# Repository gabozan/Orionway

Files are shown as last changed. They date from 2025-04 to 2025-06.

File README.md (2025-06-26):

<p align="center">
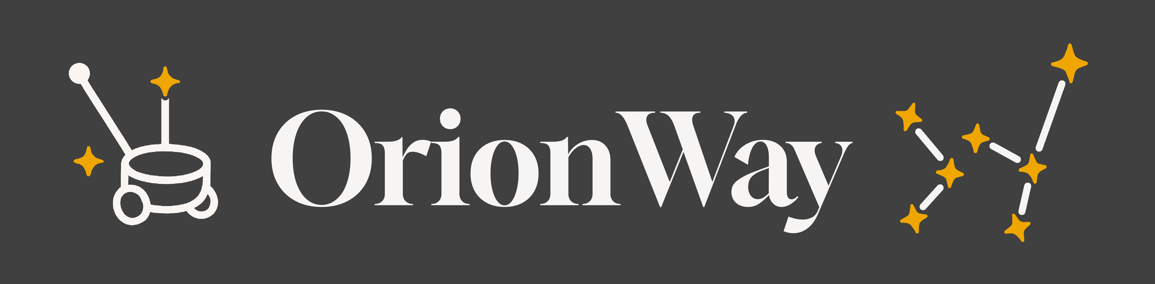
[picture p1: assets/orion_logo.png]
Logo Orionway
  
</p>

# OrionWay:  El guia robot per a trobar el teu camí 🤖👨‍🦯
&nbsp;&nbsp;&nbsp;&nbsp;

OrionWay és un **robot guia** dissenyat per acompanyar persones amb **discapacitat visual** en **entorns segurs**, com el campus de la Universitat Autònoma de Barcelona (UAB).

El projecte combina sensors i visió per computador per oferir assistència en el desplaçament, evitant perills com barreres, persones o passos de zebra. L’usuari mantindrà contacte amb el robot durant els trajectes, detectant quan el robot es desvia, dirigint-lo manualment o utilitzant-lo per identificar objectes desconeguts. L’objectiu és oferir una alternativa intermèdia entre un gos guia i el bastó blanc, combinant la seguretat i intuïció d’ambdós.

*El logotip d’OrionWay representa les inicials OW en codi Braille: ⠕⠺*

---

> [!CAUTION]
> Orionway és un prototip experimental desenvolupat en un entorn acadèmic i no està certificat per a ús assistencial en entorns reals. El seu ús com a substitut d’un gos guia o bastó blanc no està recomanat en entorns no controlats.

## 🙌 Autors
  | Nom             | NIU         |
|----------------------|-------------|
| Albert Capdevila Estadella                     | 1587933            |
| Levon Kesoyan Galstyan                      |  1668018           |
| Luis Martínez Zamora                     | 1668180            |
| Sebastian Malbaceda                      | 1681519            |
|  Gabriel Rios Sanchez                    |  1671177           |

## 🤝 Suport

### Agraïment especial
Gràcies a **Sergio Alamar**, humorista i exjugador de la selecció espanyola de futbol paralímpic, per compartir amb nosaltres la seva experiència directa com a persona cega. La seva col·laboració ens ha ajudat a identificar detalls essencials i a enfocar millor el desenvolupament d’OrionWay per fer-lo realment útil en situacions del dia a dia.

Si voleu conèixer més la seva història: [Article de La Vanguardia](https://www.lavanguardia.com/local/valencia/20250329/10522940/ciego-gracioso-sergio-alamar-comico-exolimpico.html)



### Institucions
* [Escola Enginyeria - UAB](https://www.uab.cat/ca/enginyeria)
* [UAB Open Labs](https://webs.uab.cat/openlabs/)

### Professorat
* Fernando Luis Vilariño Freire
* Vernon Stanley Albayeros Duarte
* Carlos Garcia Calvo

## 📚 Taula de continguts

- [🎥 Video demostració](#-video-demostració)
- [💫 Funcionalitats del robot OrionWay](#-funcionalitats-del-robot-orionway)
- [⚙️ Arquitectura i hardware](#️-arquitectura-i-hardware)
- [🤯 Aportacions destacades](#-aportacions-destacades-amazing-contributions)
- [🖥️ Esquemes de software](#️-esquemes-de-software)
- [🖧 Esquema de hardware](#-esquema-de-hardware)
- [📋 Requisits i instalació](#requisits-i-instalació)
- [🧪 Tests i millores](#-tests-i-milllores)
- [📚 Bibliografia i recursos](#-bibliografia-i-recursos)
- [📄 Llicència](#-llicència)

## 🎥 Video demostració
<a href="https://www.youtube.com/watch?v=D7q8VTSx6Zk">
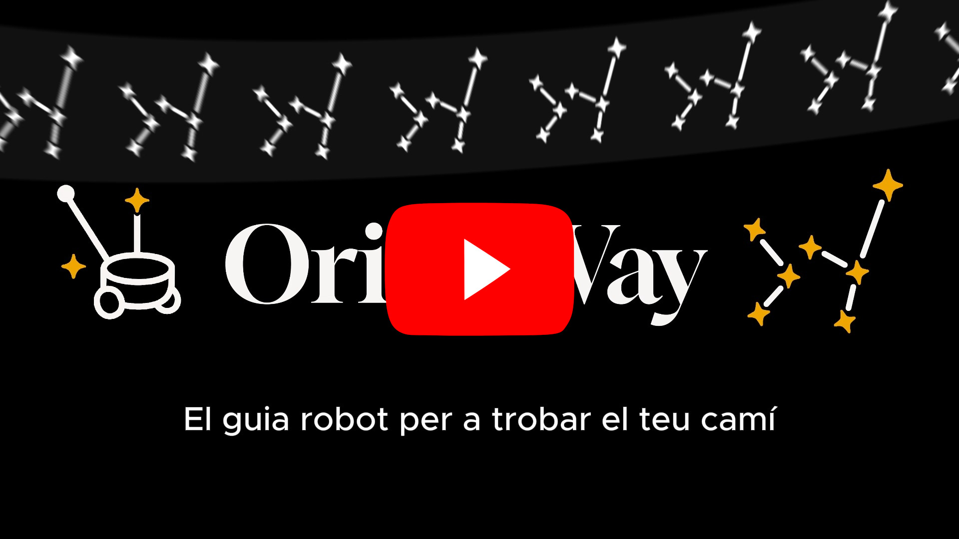
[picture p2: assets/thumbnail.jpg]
  
</a>

## 💫 Funcionalitats del robot OrionWay

| **Funcionalitat** | **Demostració** |
|---|---|
| **Detecció i reacció a obstacles immediats**<br>Mitjançant els tres sensors d'ultrasons situats al cos del robot i connectats a la placa Arduino, aquest serà capaç de detectar elements propers i modificar la trajectòria dels motors per tal d'esquivar-los. Ha de ser una funcionalitat molt ràpida i eficient, per tal d'aconseguir el millor temps de reacció. |  |
| **Detecció i reacció a passos de zebra amb semàfors**<br>Mitjançant la càmera i un model de visió per computador, podrem saber l'orientació dels passos de zebra propers, a més de detectar si els seus semàfors es troben en verd o en vermell. Això permetrà encarar el pas de zebra i creuar-lo quan pertoqui, evitant el perill. |  |
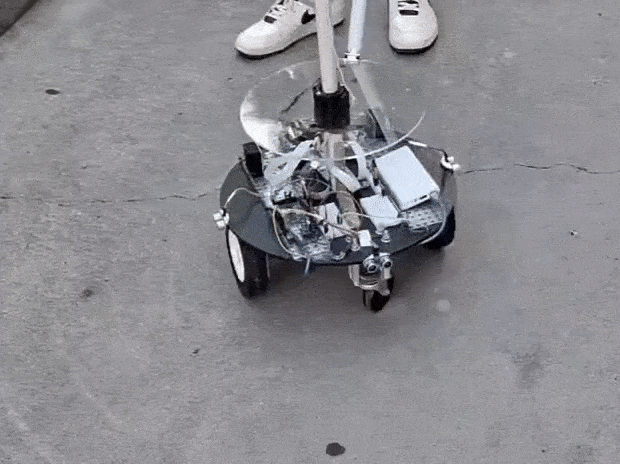
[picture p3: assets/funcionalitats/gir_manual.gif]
| **Dirigir manualment el robot en qualsevol moment**<br>En qualsevol moment dins el guiatge del robot, l'usuari podrà prémer els botons del mànec per a forçar manualment girs a la dreta o a l'esquerra. **IMPORTANT** Aquesta funcionalitat no tindrà més prioritat que les dues funcionalitats anteriors, és a dir, si a l'esquerra del robot es troba un obstacle immediat o un pas de zebra amb semàfor en vermell, el robot es detindrà. |  |
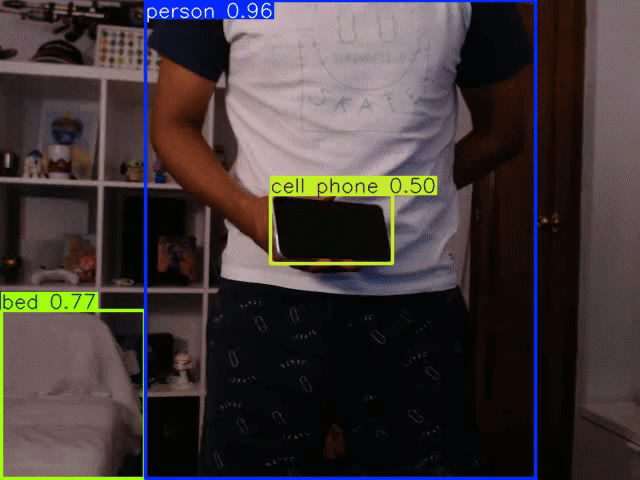
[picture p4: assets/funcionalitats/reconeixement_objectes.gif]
| **Reconeixement d'objectes i resposta per veu**<br>En qualsevol moment, l'usuari podrà preguntar al robot què subjecta a la seva mà mitjançant els botons situats al mànec. És a dir, utilitzant la càmera, el robot es detindrà, girarà la càmera, farà un reconeixement per imatge de l'objecte que l'usuari li mostri, i s'utilitzarà l'altaveu per a dir la resposta. |  |
| **Apropament automàtic cap a l'usuari en entorns tancats**<br>En situacions en què el robot té visió de l'usuari en un entorn tancat, aquest podrà ser cridat per l'usuari picant dues vegades de mans. Quan això succeeixi, el robot farà fotografies en tots els seus angles i detectarà la direcció on es troba l'usuari. Aleshores, utilitzant els sensors d'ultrasons, navegarà fins a l'usuari desplaçant-se al voltant dels obstacles que podrà trobar. |   |
   
## ⚙️ Arquitectura i hardware

L'arquitectura de software del nostre projecte está formada per:
 * Arduino
 * Python (Control Raspberry Pi)
 * YOLO (Detecció d'objectes)
 * ZebrAI (Projecte Visió per Computador que detectar semàfors i passos de zebra) [GitHub](https://github.com/albert-ce/ZebrAI-Crossing)

Respecte als components hem utilitzat el següent:
 * Arduino Mega 2560 [Datasheet](https://docs.arduino.cc/resources/datasheets/A000067-datasheet.pdf)
 * Raspberry Pi 4 4GB [Datasheet](https://www.farnell.com/datasheets/4170044.pdf)
 * Motor pas a pas 28BYJ-48 [Datasheet](https://www.mouser.com/datasheet/2/758/stepd-01-data-sheet-1143075.pdf)
 * Driver motor pas a pas ULN2003 [Datasheet](https://www.ti.com/lit/ds/symlink/uln2003a.pdf)
 * Motor 12V 455A105 [Datasheet](https://octopart.com/es/datasheet/455a105-2-globe+motors-19929790)
 * E2 optical encoder [Datasheet](https://www.usdigital.com/datasheets/e2-datasheet.pdf)
 * Sensor d'ultrasons HC-SR04 [Datasheet](https://leantec.es/wp-content/uploads/2019/06/Leantec.ES-HC-SR04.pdf)

Hem realitzar impressions 3D del següent:

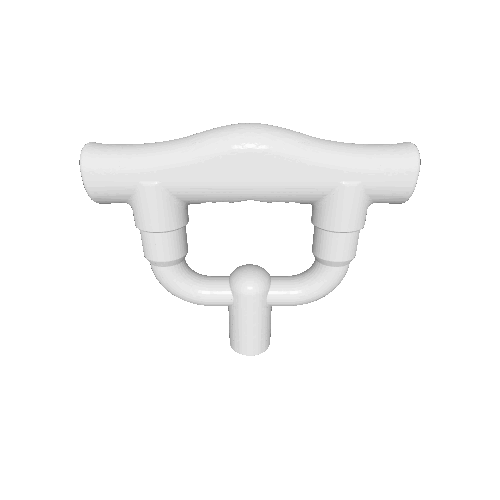
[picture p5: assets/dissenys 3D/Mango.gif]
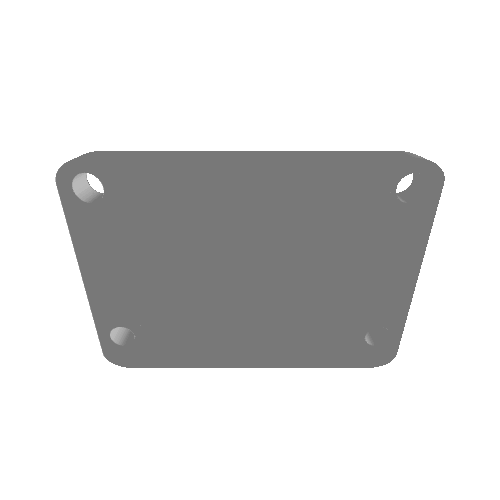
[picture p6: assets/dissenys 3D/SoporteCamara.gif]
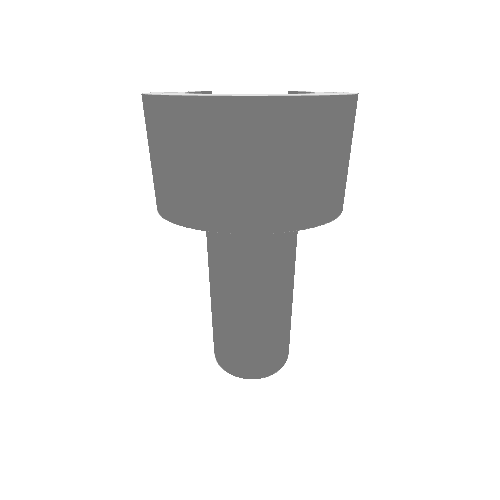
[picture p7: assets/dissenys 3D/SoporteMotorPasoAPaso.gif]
|  |  |  |
|---|---|---|
| [***Mànec***](3D%20designs/Mango.stl) | [***Suport Càmera***](3D%20designs/SoporteCamara.stl) |[***Suport Motor Pas a Pas***](3D%20designs/SoporteMotorPasoAPaso.stl)|

## 🖥️ Esquemes de software
### Casos d'us
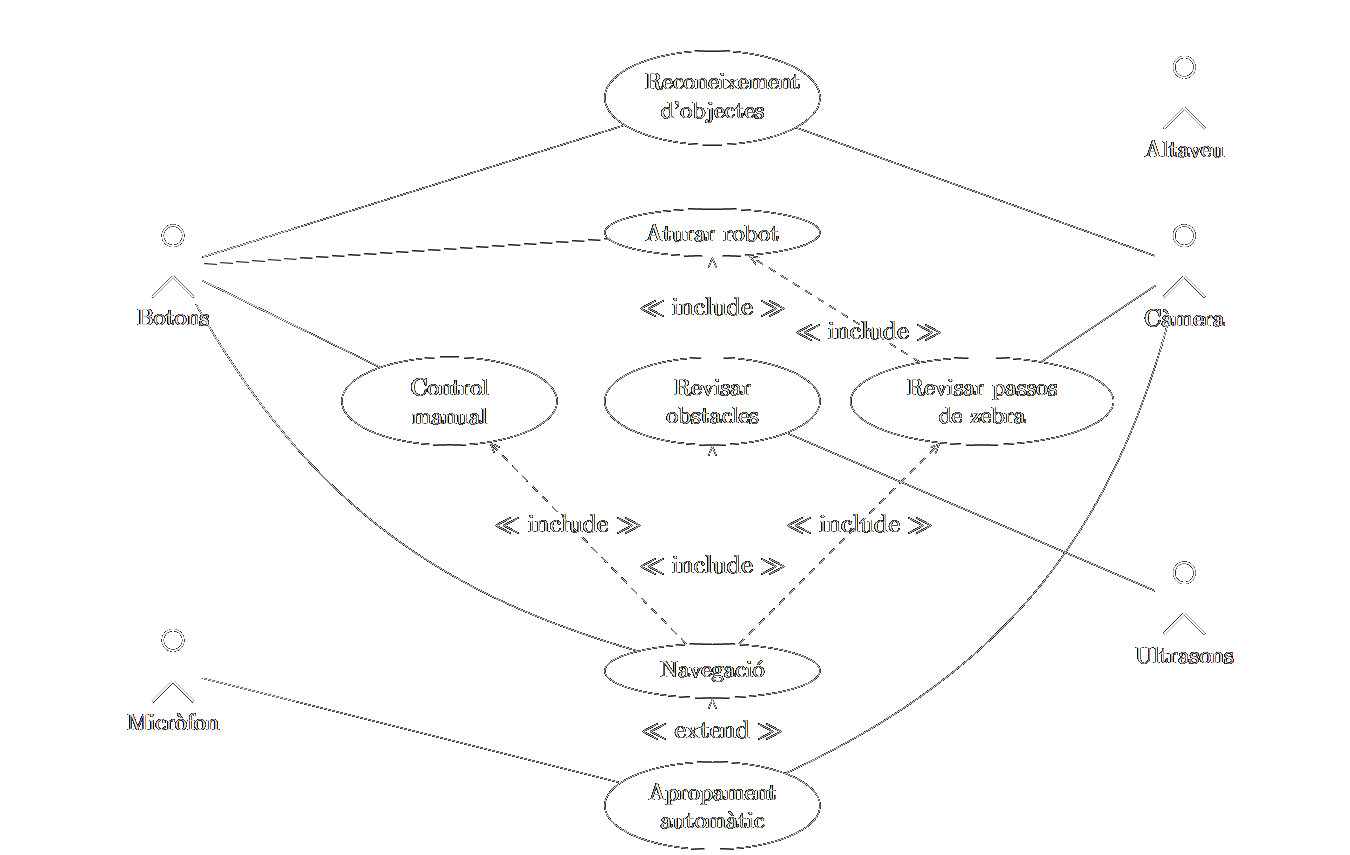
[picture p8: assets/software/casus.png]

### Mòduls
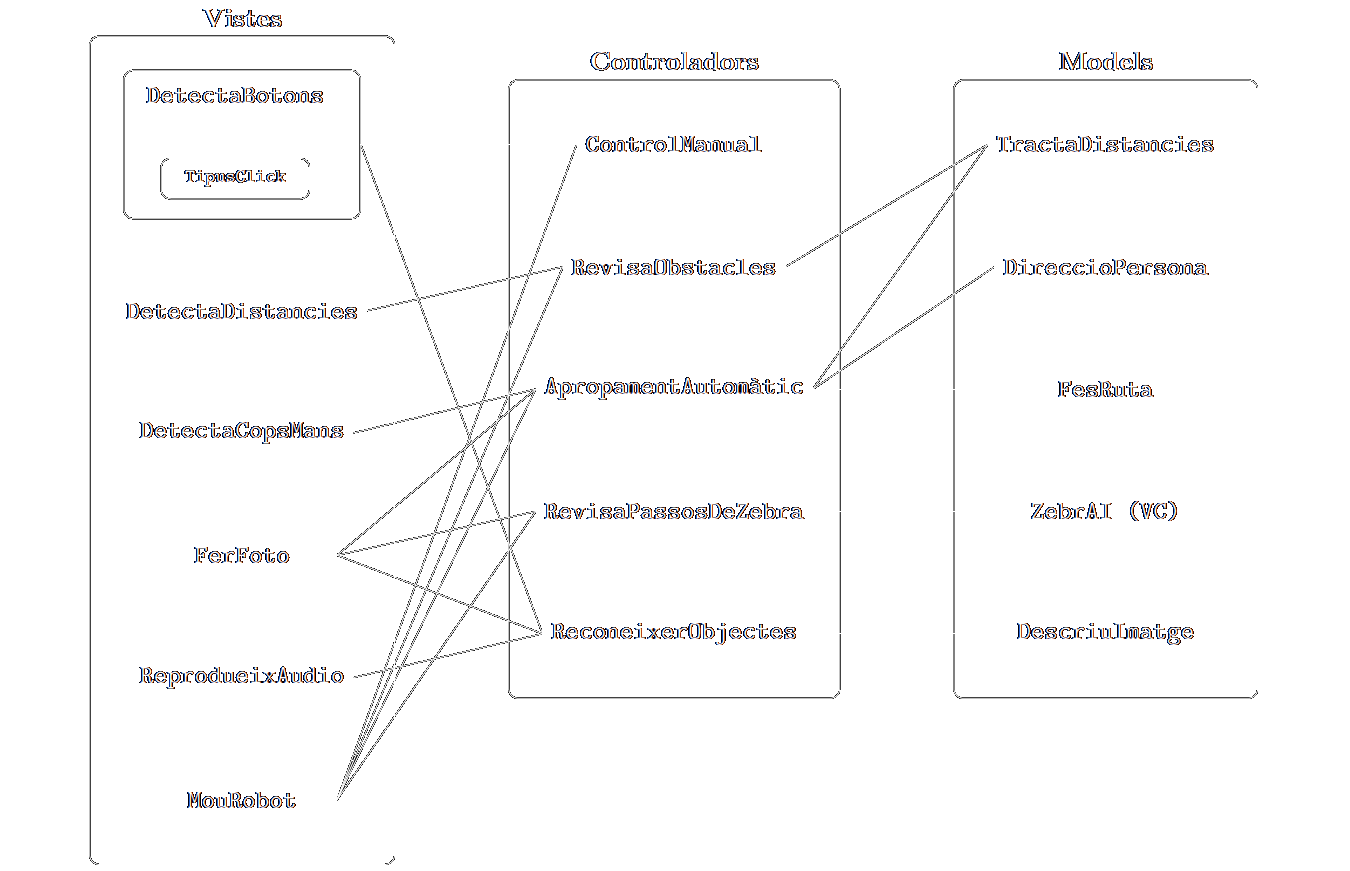
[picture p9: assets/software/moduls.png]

### Estats
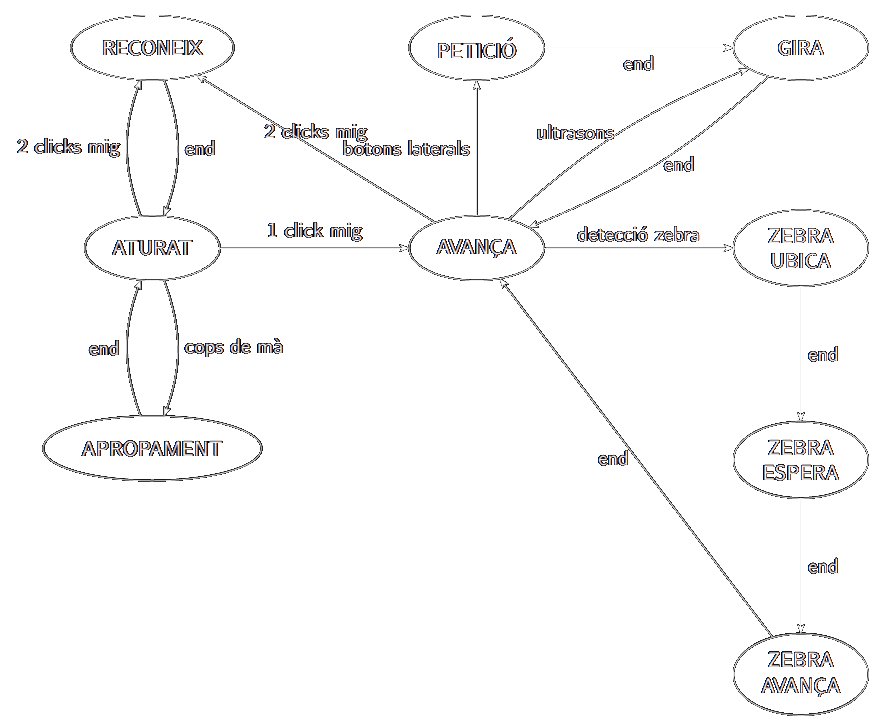
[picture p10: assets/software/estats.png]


### 🖧 Esquema de hardware
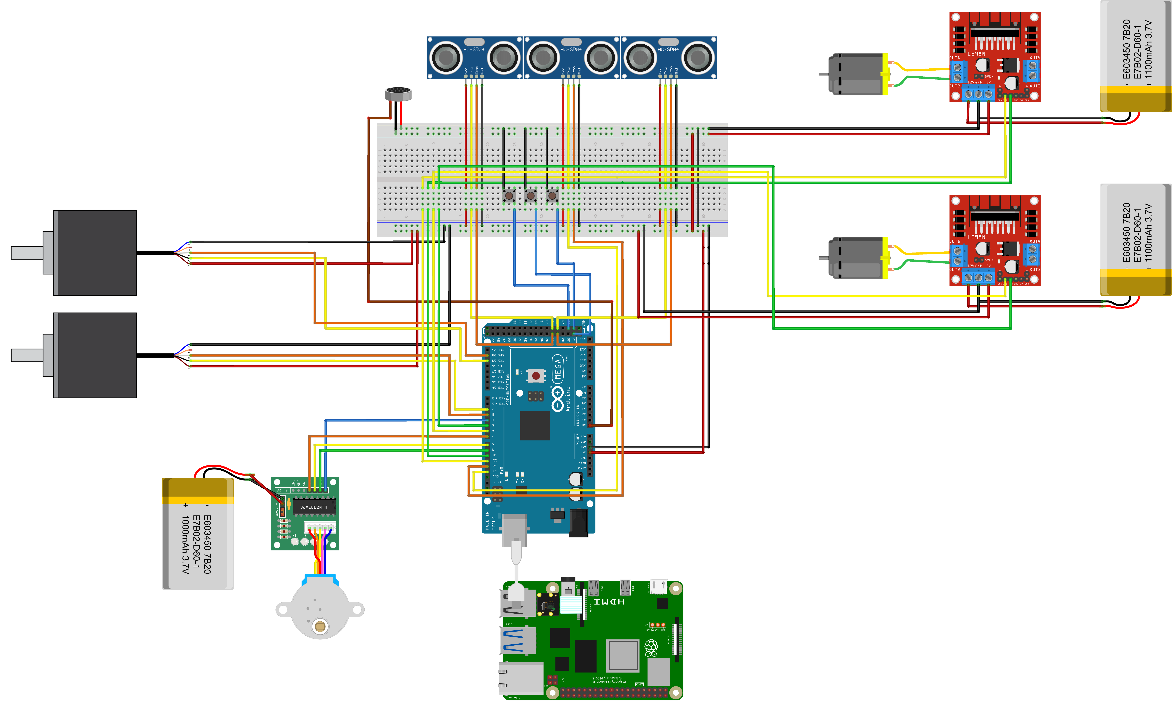
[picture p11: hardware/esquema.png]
  

## 🤯 Aportacions destacades (Amazing contributions)
* Robot guia intel·ligent per a persones amb discapacitat visual.
* Disseny i impressió 3D de components personalitzats i funcionals.
* Reconeixement avançat de passos de vianants amb semàfor mitjançant visió per computador clàsica i moderna.
* Identificació *on-demand* d’objectes particulars amb resposta per veu.
* API al núvol per a un processament d’imatges ràpid i escalable.
* Arquitectura modular i adaptable a noves funcionalitats.
* Codi i models d’intel·ligència artificial 100% oberts i reutilitzables.

## 📋Requisits i instalació
- **Python**: 3.10 
- **Sistema operatiu**:
  - Per a `cloud-api`: Linux recomanat 
  - Per a `raspberry`: Raspbian o similar en Raspberry Pi.

### Requisits per a `cloud-api`

#### Dependències de Python

```bash
flask==3.1.1
gunicorn==23.0.0
ultralytics==8.3.111
opencv-python-headless==4.10.0.84
numpy==2.1.1
torch>=1.8.0
torchvision>=0.9.0
pillow>=10.3.0
PyYAML>=5.3.1
requests>=2.32.2
tqdm>=4.66.3
pandas>=1.1.4
```

#### Dependències del sistema (Linux)

```bash
sudo apt-get update && sudo apt-get install 
```

### Requisits per a `raspberry`

#### Dependències de Python

```bash
pyserial==3.5
picamera2==0.0.5
opencv-python==4.9.0.80
numpy==1.24.4
requests==2.31.0
google-cloud-texttospeech==2.15.1
pygame==2.1.3
```

---

### Instal·lació ràpida

#### 1. Clona el repositori

```bash
git clone https://github.com/gabozan/Orionway
cd Orionway
```

#### 2. Instal·la Python 3.10 i pip si no els tens

#### 3. Instal·la les dependències per a cada subprojecte

##### Per a `cloud-api`:

```bash
cd cloud-api
pip install -r requirements.txt
```

##### Per a `raspberry`:

```bash
cd raspberry
pip install -r requirements.txt
```

#### 4. Obre el projecte a l'IDE d'Arduino i puja'l a la placa

```bash
cd arduino
```

1. Obre l'arxiu main.ino amb l’IDE d’Arduino.
2. A l'IDE, selecciona la teva placa i tria el port corresponent.
3. Compila per pujar el codi a la placa.

---

## 🧪 Tests i milllores
  * En aquest projecte s'han fet una serie de tests per tal de comprovar que el funcionament es com esperem que sigui, totes aquestes proves es troben en [Tests](/docs/Tests.pdf)
  * Per altra banda, en aquest projecte hem tingut en compte unes posibles millores que té l'utilització del robot, tots aquests els hem recopilat en [Millores](/docs/Millores.pdf)

## 📚 Bibliografia i recursos
* [*Problemas y requisitos en el diseño de un robot de guiado para personas ciegas y mayores*](https://publicaciones.asoc-aeim.es/anales/article/view/32/220)
* [*Una revisión de sistemas asistenciales basados en visión para personas con discapacidad visual: tecnologías, aplicaciones y direcciones futuras.*](https://chatpaper.com/es/chatpaper/paper/138956)
* [*Documentació oficial d'Arduino*](https://docs.arduino.cc/language-reference/)

### 📄 Llicència
  Aquest projecte està llicenciat sota la Llicència MIT.

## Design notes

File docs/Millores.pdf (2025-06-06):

# Document de millores

Aquest document exposa les millores addicionals que es podrien implementar en el nostre complex projecte. Amb una major inversió de temps i pressupost, el nostre robot podria assolir capacitats superiors. A continuació, es detallen les millores que han quedat pendents de realització:

- Seguretat: Incorporar més sensors de proximitat a la base del robot per a la detecció de desnivells, prevenint així caigudes tant del dispositiu com de l'usuari.
- Navegació per veu: Implementar un sistema de reconeixement de veu que permeti a l'usuari indicar el destí. Integració amb serveis de geolocalització i APIs de mapes (com Google Maps) per al guiatge autònom del robot..
- Anticipació i prevenció d'obstacles: Incorporar un sistema de detecció d'obstacles amb un rang de detecció més ampli. Aquesta millora permetrà predir els moviments de l'entorn, com el desplaçament de persones, i seleccionar la ruta més segura per a l'usuari.
- Actuació pas de zebra: Si un pas de zebra no té semàfor, cal verificar que els vehicles, en cas de que hi hagin, s'aturin per permetre el pas dels vianants abans de creuar.

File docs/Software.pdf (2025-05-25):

# Diagrames de Software

## RLP - Grup 5

### 25 de maig de 2025

## Diagrama de casos d’´us

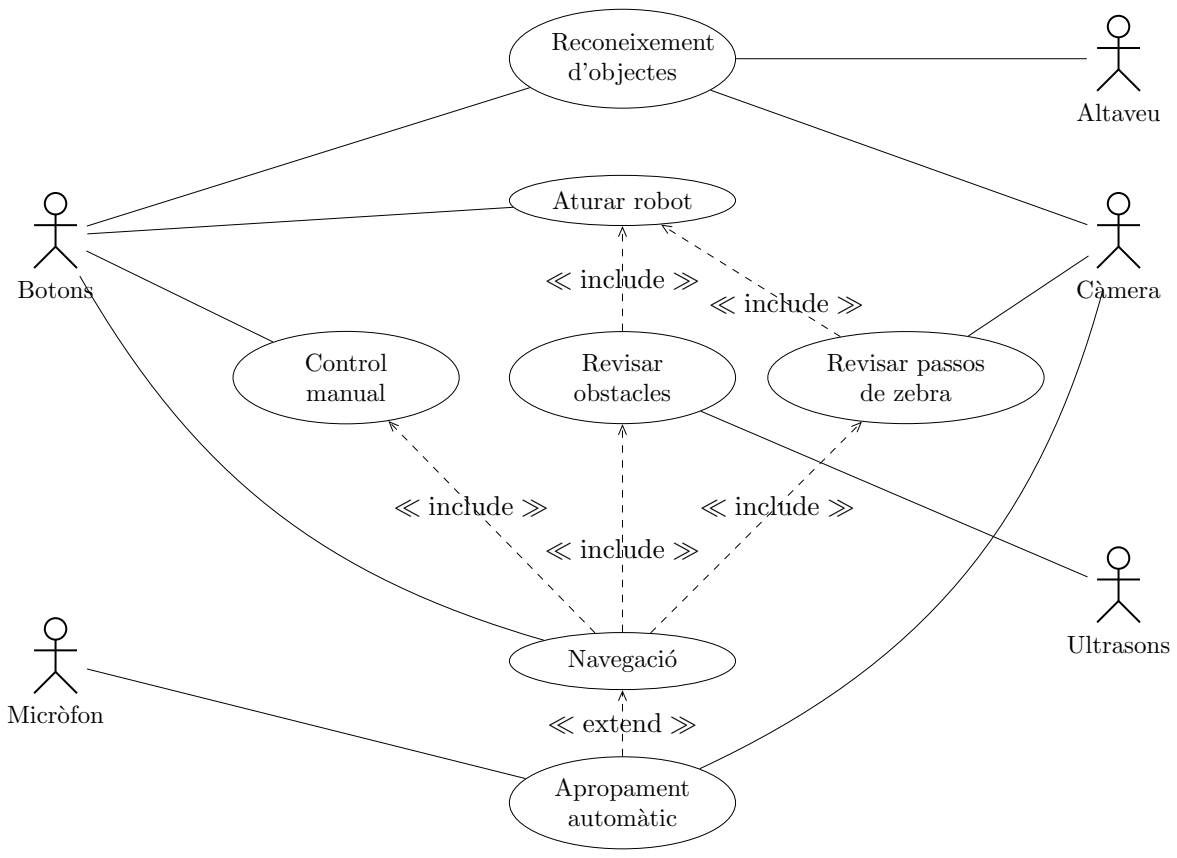
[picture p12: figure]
Reconeixement d’objectes; Aturar robot; Control manual; Revisar obstacles; Revisar passos de zebra; Navegaci´o; Apropament autom`atic; Botons; Ultrasons; C`amera; Altaveu; Micr`ofon; ≪ extend ≫; ≪ include ≫

1

## Diagrama de m`oduls

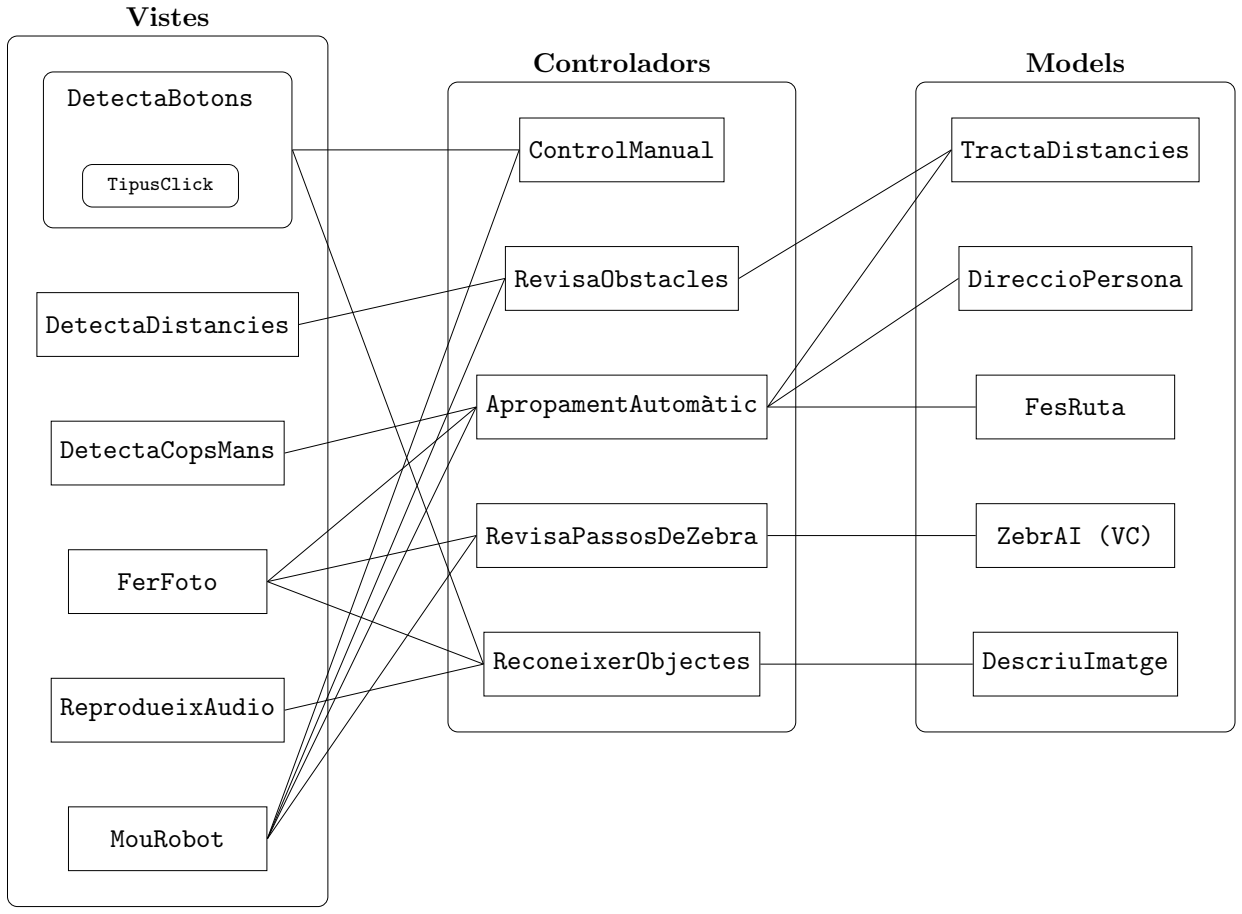
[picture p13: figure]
DetectaBotons; TipusClick; DetectaDistancies; DetectaCopsMans; FerFoto; ReprodueixAudio; MouRobot; Vistes; ControlManual; RevisaObstacles; ApropamentAutom`atic; RevisaPassosDeZebra; ReconeixerObjectes; Controladors; TractaDistancies; DireccioPersona; FesRuta; ZebrAI (VC); DescriuImatge; Models

2

## Diagrama d’estats

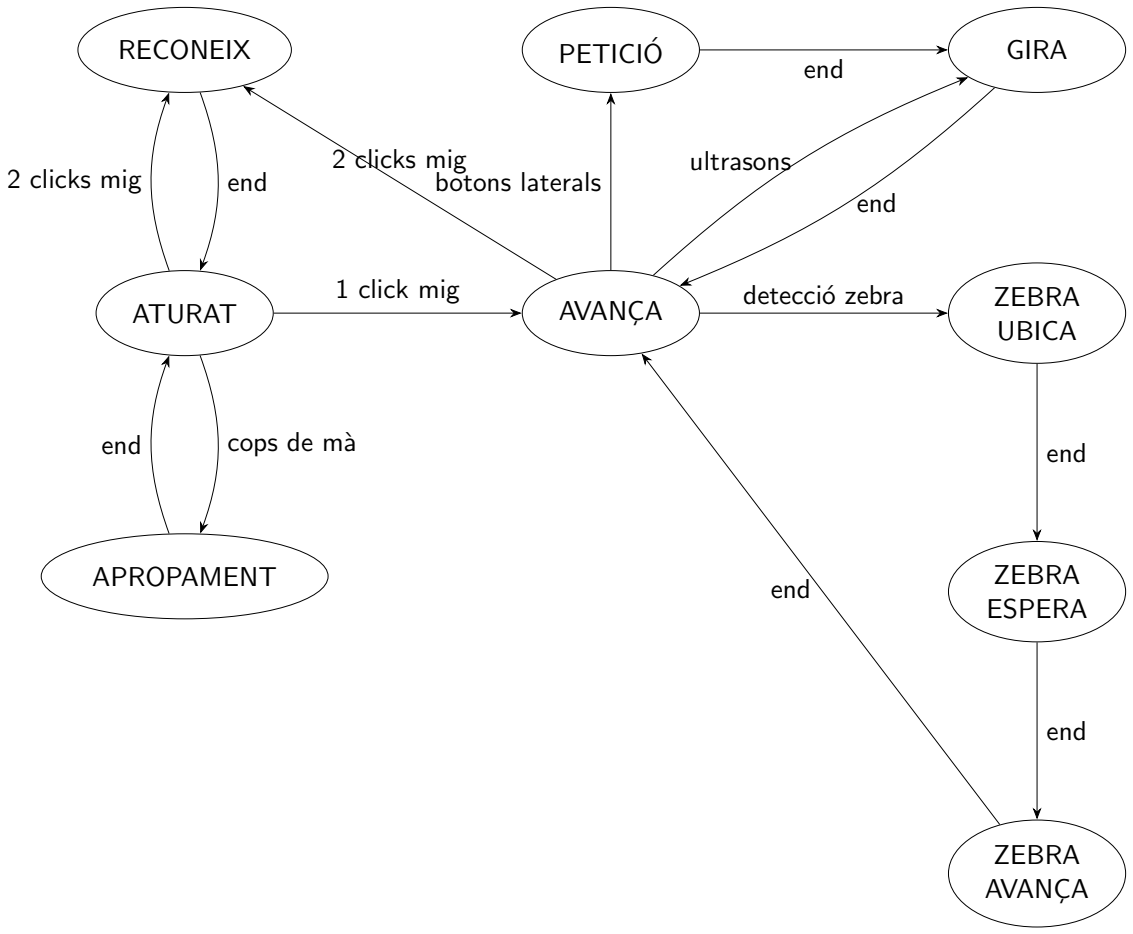
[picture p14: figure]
RECONEIX; ATURAT; AVANC¸A; APROPAMENT; PETICIO´; ZEBRA UBICA; ZEBRA ESPERA; ZEBRA AVANC¸A; GIRA; end; 1 click mig; 2 clicks mig; cops de m`a; ultrasons; botons laterals; detecci´o zebra

3

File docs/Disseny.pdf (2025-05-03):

# Disseny inicial

### RLP - Grup 5

### 14 d’abril de 2025

### Introducció

OrionWay és un robot dissenyat per oferir assistència a persones amb discapacitat visual. Aquest ajudarà aquestes persones a desplaçar-se pel carrer evitant els perills existents (barreres, persones, travessar passos de zebra...).
L’usuari estarà en contacte amb el robot durant els trajectes, notant quan aquest es desvia, dirigint-lo manualment, o inclús utilitzant-lo per a identificar objectes desconeguts.

### Especificació

Les funcionalitats que tindrà OrionWay seran:

| Detecció i reacció a obstacles immediats
| Detecció i reacció a passos de zebra amb semàfors
| Dirigir manualment el robot en qualsevol moment
| Reconeixement d’objectes i resposta per veu
| Apropament automàtic cap a l’usuari en entorns tancats
| Guiatge cap a ubicacions marcades en un mapa.

Detecció i reacció a obstacles immediats

Mitjançant els tres sensors d’ultrasons situats al cos del robot i connectats a la placa Arduino, aquest serà capaç de detectar elements propers i modificar la trajectòria dels motors per tal d’esquivar-los. Ha de ser una funcionalitat molt ràpida i eficient, per tal d’aconseguir el millor temps de reacció.

Detecció i reacció a passos de zebra amb semàfors

Mitjançant la càmera i un model de visió per computador, podrem saber l’orientació dels passos de zebra propers, a més de detectar si els seus semàfors es troben en verd o en vermell. Això permetrà encarar el pas de zebra i creuar-lo quan pertoqui, evitant el perill.

Dirigir manualment el robot en qualsevol moment

En qualsevol moment dins el guiatge del robot, l’usuari podrà prémer els botons del mànec per a forçar manualment girs a la dreta o a l’esquerra. IMPORTANT: Aquesta funcionalitat no tindrà més prioritat que les dues funcionalitats anteriors, és a dir, si a l’esquerra del robot es troba un obstacle immediat o un pas de zebra amb semàfor en vermell, el robot es detindrà.

1

Reconeixement d’objectes i resposta per veu

En qualsevol moment, l’usuari podrà preguntar al robot què subjecta a la seva mà mitjançant els
botons situats al mànec. Es a dir, utilitzant la càmera, el robot es detindrà, girarà la càme ´ | ra, farà
un reconeixement per imatge de l’objecte que l’usuari li mostri, i s’utilitzarà l’altaveu per a dir la resposta.

Apropament automàtic cap a l’usuari en entorns tancats

En situacions en què el robot té visió de l’usuari en un entorn tancat, aquest podrà ser cridat per l’usuari picant dues vegades de mans. Quan això succeeixi, el robot farà fotografies en tots els seus angles i detectarà la direcció on es troba l’usuari. Aleshores, utilitzant els sensors d’ultrasons, navegarà fins a l’usuari desplaçant-se al voltant dels obstacles que podrà trobar.

2

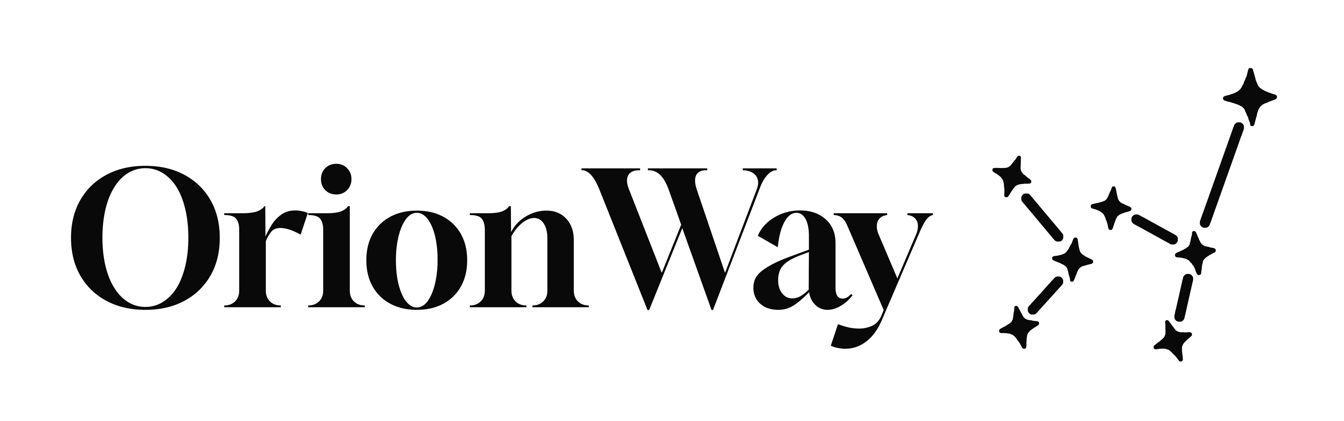
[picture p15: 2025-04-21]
assets/orionway.JPG

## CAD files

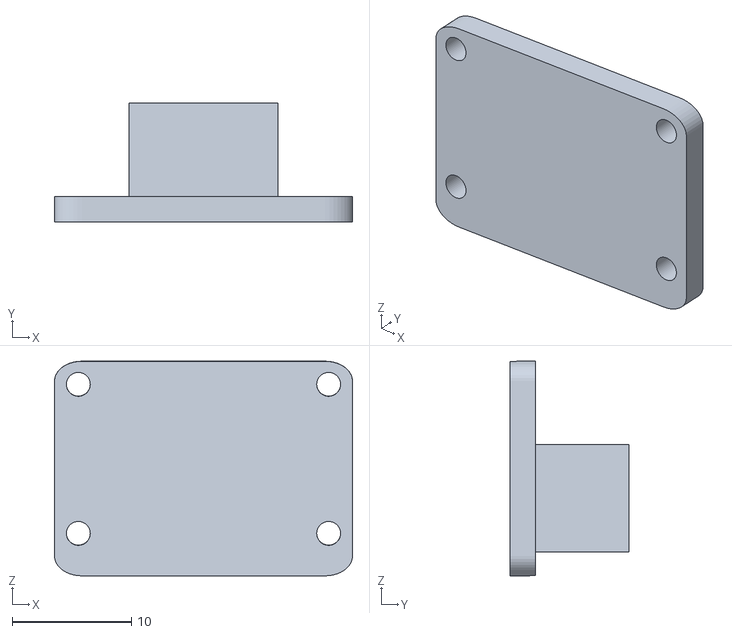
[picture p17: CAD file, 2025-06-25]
3D designs/SoporteCamara.stl
25.0 x 10.0 x 18.0

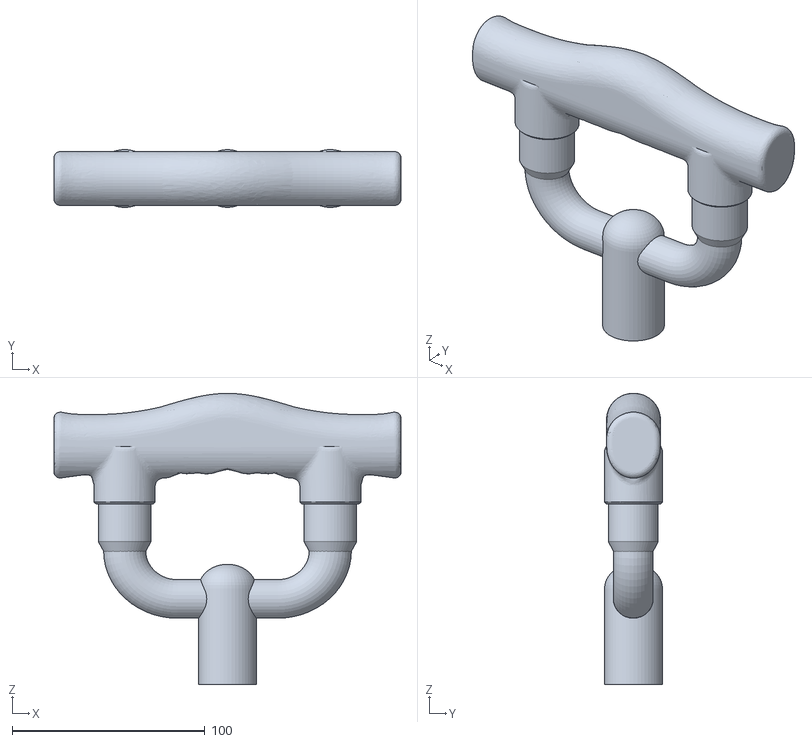
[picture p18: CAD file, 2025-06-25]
3D designs/Mango.stl
180.0 x 30.0 x 151.2

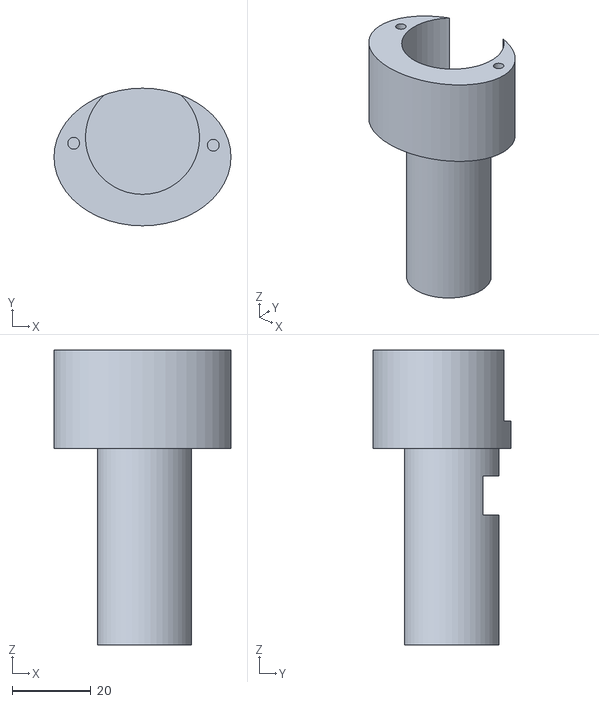
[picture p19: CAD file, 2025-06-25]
3D designs/SoporteMotorPasoAPaso.stl
45.0 x 35.0 x 75.0

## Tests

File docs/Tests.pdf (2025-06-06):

# Document de tests

## Tests de canvi d'estat

- Test de funcionament de sensors d'ultrasò
- Detecció correcta de distància a un obstacle.
En cas que la distància sigui menor al valor que considerem suficient per seguir treballant es canvia de l'estat “Avança” a l'estat “Gira”.
- Test de funcionament de cadascun dels botons
- Detecció correcta d'una pulsació
- Detecció correcta de dues pulsacions
- Detecció correcta de mantenir premut

Per a cada un dels botons hi ha un canvi d'estat específic, mostrat a la taula següent.

Estat actual | Interacció | Estat següent
Avança | Pulsació simple lateral | Petició
Avança/Aturat | Dues pulsacions centrals | Reconeix
Aturat | Pulsació simple central | Avança
- Prova de comprovació del micròfon
- Detecció correcta de palmades quan es cridi el robot

En cas que es detectin dues palmades, es passarà de l'estat “Aturat” a “Apropament”.

- Test de càmera/imatges
- Detecció correcta de passos de zebra i/o semàfors, la qual cosa provocarà un canvi d'estat d’"Avança" a "Zebra ubica", on s'aplicarà tota la lògica per extremar la precaució en acostar-se a un pas de zebra.

## Altres tests

- Test de funcionament de l'altaveu
- Comunicació correcta de manera comprensible
- Test de moviment correcte de motors de rodes
- Canvi de velocitat correcte quan cal extremar la precaució.
- Canvi correcte de direcció en esquivar obstacles o canviar de direcció.

- Test de hardware
- Intercomunicació correcta entre Arduino i Raspberry Pi.
- Comprovació de la durabilitat del robot en aplicar una força feta per una persona en moviment.
- Test de detecció correcta.
- Durant l'estat “Reconeix” es comprova que detecti correctament l'objecte que hi ha a la vista de la càmera. Ho comprovem de la manera següent:
- De la mateixa manera, durant l'estat “Apropament”, en el qual el robot s'acosta a l'usuari, detectem si hi ha una persona a la imatge i si aquesta és a prop. Ho comprovem de la manera següent:

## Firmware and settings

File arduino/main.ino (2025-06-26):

int angleStartFromFOV();
float offsetToAngle(int offset, int resolution = 640, float fov = 62.0);
// void rotateCameraToCenter(); 


// ---------------------------------------- buttons_control.ino
const int buttonPins[3] = { 51, 52, 53 };
int estatActual[3] = { HIGH, HIGH, HIGH };
int estatAnterior[3] = { HIGH, HIGH, HIGH };
unsigned long lastPressTime[3] = { 0, 0, 0 };
int clickCount[3] = { 0, 0, 0 };
unsigned long lastReleaseTime[3] = { 0, 0, 0 };
unsigned long holdStartTime[3] = { 0, 0, 0 };
int clickState[3] = { 0, 0, 0 };

const long debounceDelay = 50;
const long doubleClickInterval = 300;
const long holdTimeThreshold = 3000;

typedef enum
{
  BUTTON_NONE = -1,
  BUTTON0_SINGLE_CLICK = 0,
  BUTTON1_SINGLE_CLICK = 1,
  BUTTON2_SINGLE_CLICK = 2,
  BUTTON0_LONG_PRESS = 10,
  BUTTON1_LONG_PRESS = 11,
  BUTTON2_LONG_PRESS = 12,
  BUTTON1_DOUBLE_CLICK = 21
} ButtonEvent;

// ---------------------------------------- detect_distances.ino
const int trigPins[3] = { 45, 13, 47 };
const int echoPins[3] = { 44, 12, 46 };
const int thresholds[3] = { 30, 30, 30 };

float distancies[3];

// Màquina d’estats per sensor
enum EstatSensor { IDLE, TRIGGER, ESPERANT_HIGH, ESPERANT_LOW, CALCULAT };

const unsigned long timeoutEcho = 30000;
bool objectesDetectats[3];


// ---------------------------------------- motors.ino
#include <RotaryEncoder.h>

#define LPWM1 10
#define LPWM2 11
#define RPWM1 5
#define RPWM2 6

#define LEFT_CHA 19
#define LEFT_CHB 20
#define RIGHT_CHA 2
#define RIGHT_CHB 3

const long TICKS_PER_REV = 50000;
const float r = 7.25; // cm
const float d = 15.0; // cm
const uint8_t linealPWM = 50;
const uint8_t rotatoryPWM = 80;

RotaryEncoder leftEncoder(LEFT_CHA, LEFT_CHB, RotaryEncoder::LatchMode::TWO03);
RotaryEncoder rightEncoder(RIGHT_CHA, RIGHT_CHB, RotaryEncoder::LatchMode::TWO03);

// ---------------------------------------- detect_clap.ino
const int micPin = A0;
const int soundThreshold = 50;
const unsigned long minTimeGap = 200;
const unsigned long maxTimeGap = 500;
unsigned long previousTapTime = 0;
unsigned long timeSinceLastTap = 0;

// ---------------------------------------- stepper.ino

const int IN1 = 4;   // módulo IN1
const int IN2 = 9;   // módulo IN2
const int IN3 = 8;   // módulo IN3
const int IN4 = 7;   // módulo IN4

const int STEPS_PER_REV = 4096;  // pasos totales
const int STEP_DELAY = 3000;     // velocidad

const int stepSequence[8][4] = {
  {1, 0, 0, 0},
  {1, 1, 0, 0},
  {0, 1, 0, 0},
  {0, 1, 1, 0},
  {0, 0, 1, 0},
  {0, 0, 1, 1},
  {0, 0, 0, 1},
  {1, 0, 0, 1}
};

int absolutePosition = 0;

typedef enum {
  ATURAT,
  RECONEIX,
  AVANCA,
  GIRA,
  PETICIO,
  ZEBRA_ESPERA,
  ZEBRA_UBICA,
  ZEBRA_AVANCA,
  APROPAMENT_SEARCH_PERSON,
  APROPAMENT_ORIENT_ROBOT,
  APROPAMENT_FORWARD_TO_OBSTACLE,
  APROPAMENT_CHECK_ARRIVAL,
  APROPAMENT_AVOID_OBSTACLE,
} RobotState;

RobotState estat = ATURAT;
ButtonEvent button = BUTTON_NONE;
RobotState giraSeguent = ATURAT;
float angle = 0;
int instruccio;

// APROPAMENT: variables
int  scanAngle = angleStartFromFOV();           // angle actual de barrida
unsigned long lastScanTs = 0;                   // temporitzador de camera
int  foundAngle = 0;                            // angle relatiu a la persona
float offset = 0;
uint16_t bbWidth = 0;                           // bounding‑box
int  avoidTurnDeg = 0;                          // +90 / –90  (esquerra / dreta)
bool instructionSent = false;                   // indica si s'ha enviat la instrucció a la Raspberry

const char* robotStateToString(RobotState state) {
  switch (state) {
  case ATURAT:                      return "ATURAT    ";
  case RECONEIX:                    return "RECONEIX  ";
  case AVANCA:                      return "AVANCA    ";
  case GIRA:                        return "GIRA      ";
  case PETICIO:                     return "PETICIO   ";
  case ZEBRA_ESPERA:               return "ZEB_ESPERA";
  case ZEBRA_UBICA:                return "ZEB_UBICA ";
  case ZEBRA_AVANCA:               return "ZEB_AVANCA";
  case APROPAMENT_SEARCH_PERSON:    return "APR_SEARCH";
  case APROPAMENT_ORIENT_ROBOT:     return "APR_ORIENT";
  case APROPAMENT_FORWARD_TO_OBSTACLE: return "APR_FORWD";
  case APROPAMENT_CHECK_ARRIVAL:    return "APR_CHECK ";
  case APROPAMENT_AVOID_OBSTACLE:   return "APR_AVOID ";
  default:                          return "DESCONEGUT";
  }
}

void setup()
{
  initDistancies();
  initButtons();
  initRaspberryIO();
  initMotors();
  initStepperCam();
}

void loop()
{
  unsigned long currentTime = millis();
  button = getButtons();
  RevisaObstacles();
  // Serial.println(readInput());
  Serial.print("\rEstat: ");
  Serial.print(robotStateToString(estat));
  Serial.print(" | Button: ");
  Serial.print(button);
  Serial.print(" | Left: ");
  Serial.print(objectesDetectats[0]);
  Serial.print(" | Front: ");
  Serial.print(objectesDetectats[1]);
  Serial.print(" | Right: ");
  Serial.print(objectesDetectats[2]);
  Serial.print(" | Distances: ");
  Serial.print(distancies[0]);
  Serial.print(", ");
  Serial.print(distancies[1]);
  Serial.print(", ");
  Serial.print(distancies[2]);
  Serial.print(" | Micròfon: ");
  Serial.println(readInput());
  switch (estat) {

    //=====================//
    //       ATURAT        //
    //=====================//
  case ATURAT:
    //--------------[ ACCIONS ]--------------
    stopMotors();

    //-----------[ CANVIS D'ESTAT ]----------

    // Dos cops de mans
    if (getTaps())
    {
      estat = APROPAMENT_SEARCH_PERSON;
      break;
    }

    // Pulsació al botó central (una o dues vegades)
    switch (button) {
    case BUTTON1_SINGLE_CLICK:
      estat = AVANCA;
      moveForward();
      break;
    case BUTTON1_DOUBLE_CLICK:
      estat = RECONEIX;
      rotateCamera(PI);
      sendInstructionToRaspberry(RECONEIX);
      break;
    }

    break;

    //=====================//
    //      RECONEIX       //
    //=====================//
  case RECONEIX:

    //-----------[ CANVIS D'ESTAT ]----------

    // La Raspberry retorna el següent codi = Ha acabat correctament
    if (readInstructionFromRaspberry() == ATURAT)
    {
      rotateCamera(-PI);
      estat = ATURAT;
      break;
    }
    break;

    //=====================//
    //       AVANCA        //
    //=====================//
  case AVANCA:
    //--------------[ ACCIONS ]--------------
    // moveForward();

    //-----------[ CANVIS D'ESTAT ]----------
    // Detectar parets davant
    // RevisaObstacles(objectesDetectats);
    if (objectesDetectats[1])
    {
      angle = objectesDetectats[2] ? -PI / 2 : PI / 2;  // En cas que la dreta no estigui lliure, gira a l'esquerra (no contemplat cas on hi ha d'haver gir 180º)
      estat = GIRA;
      giraSeguent = AVANCA;
      break;
    }

    // Pulsació al botó central (una o dues vegades)
    switch (button) {
    case BUTTON0_LONG_PRESS:
    case BUTTON2_LONG_PRESS:
      estat = PETICIO;
      break;
    case BUTTON1_SINGLE_CLICK:
      estat = ATURAT;
      break;
    case BUTTON1_DOUBLE_CLICK:
      estat = RECONEIX;
      sendInstructionToRaspberry(RECONEIX);
      break;
    }

    // Reconeixement de pas de zebra
    instruccio = readInstructionFromRaspberry();
    if (instruccio == ZEBRA_UBICA)
    {
      estat = ZEBRA_UBICA;
      break;
    }

    break;

    //=====================//
    //      PETICIO       //
    //=====================//
  case PETICIO:
    //-----------[ CANVIS D'ESTAT ]----------
    // RevisaObstacles(objectesDetectats);  // Es pot treure si veiem que a AVANCA ja es fa i no fa falta repetir-ho

    // Si no es detecten obstacles en la direcció de la PETICIO
    if ((!objectesDetectats[0] && button == BUTTON0_LONG_PRESS) || (!objectesDetectats[2] && button == BUTTON2_LONG_PRESS))
    {
      angle = button == BUTTON0_LONG_PRESS ? -PI / 2 : PI / 2;
      estat = GIRA;
      giraSeguent = AVANCA;
      break;
    }
    else
    {
      estat = AVANCA;
      moveForward();
      break;
    }
    break;


    //=====================//
    //        GIRA         //
    //=====================//
  case GIRA:
    rotate(angle);
    estat = giraSeguent;
    if (estat == AVANCA) moveForward();
    break;

    //========================//
    //      ZEBRA_UBICA       //
    //========================//
  case ZEBRA_UBICA:

    //-----------[ CANVIS D'ESTAT ]----------
    instruccio = readInstructionFromRaspberry();
    if (instruccio == ZEBRA_ESPERA)
    {
      estat = ZEBRA_ESPERA;
      break;
    }
    break;

    //========================//
    //      ZEBRA_ESPERA      //
    //========================//
  case ZEBRA_ESPERA:

    //-----------[ CANVIS D'ESTAT ]----------
    instruccio = readInstructionFromRaspberry();
    if (instruccio == ZEBRA_AVANCA)
    {
      estat = ZEBRA_AVANCA;
      moveForward();
      break;
    }
    break;

    //========================//
    //      ZEBRA_AVANCA      //
    //========================//
  case ZEBRA_AVANCA:
    //--------------[ ACCIONS ]--------------
    // moveForward();

    //-----------[ CANVIS D'ESTAT ]----------
    instruccio = readInstructionFromRaspberry();
    if (instruccio == AVANCA)
    {
      estat = AVANCA;
      moveForward();
      break;
    }
    break;

    //========================//
    //      APROPAMENT        //
    //========================//
  case APROPAMENT_SEARCH_PERSON:
    if (!instructionSent) {
      // Enviem la instrucció a la Raspberry per iniciar la cerca de la persona
      sendInstructionToRaspberry(APROPAMENT_SEARCH_PERSON);
      instructionSent = true;
    }
    if (hasElapsed(lastScanTs)) {
      rotateCamera(scanAngle);
      scanAngle = nextScanAngle(scanAngle);
      if (hasCompletedScan(scanAngle)) {
        //No es troba ningú després de fer barrida completa --> torna a ATURAT
        estat = ATURAT;
        instructionSent = false;
        break;
      }
      lastScanTs = millis();
    }
    estat = APROPAMENT_ORIENT_ROBOT;
    break;

  case APROPAMENT_ORIENT_ROBOT:
    instruccio = readInstructionFromRaspberry();
    //tornem a detectar la persona
    if (instruccio == APROPAMENT_SEARCH_PERSON)
    {
      estat = APROPAMENT_SEARCH_PERSON;
      instructionSent = false;
      break;
    }
    offset = readFloatFromRaspberry();
    if (offset == NAN) {
      estat = ATURAT;
      instructionSent = false;
      break;
    }
    foundAngle = offsetToAngle(offset);
    rotateCameraToCenter();
    rotate(foundAngle);
    moveForward();
    estat = APROPAMENT_FORWARD_TO_OBSTACLE;
    instructionSent = false;
    break;

  case APROPAMENT_FORWARD_TO_OBSTACLE:
    RevisaObstacles();
    if (objectesDetectats[1]) {
      stopMotors();
      estat = APROPAMENT_CHECK_ARRIVAL;
      instructionSent = false;
    }
    break;

  case APROPAMENT_CHECK_ARRIVAL:
    if (!instructionSent) {
      // Enviem la instrucció a la Raspberry per comprovar si hi ha una persona a prop
      sendInstructionToRaspberry(APROPAMENT_CHECK_ARRIVAL);
      instructionSent = true;
    }

    instruccio = readInstructionFromRaspberry();
    if (instruccio == APROPAMENT_CHECK_ARRIVAL) {
      // Persona trobada, i a prop. Fi de l'apropament
      stopMotors();
      estat = ATURAT;
      instructionSent = false;
      rotateCameraToCenter();
      scanAngle = angleStartFromFOV();
      rotate(180); // Gira 180º per tornar a la posició inicial
    }
    else if (instruccio == APROPAMENT_AVOID_OBSTACLE) {
      // No es una persona
      avoidTurnDeg = (objectesDetectats[0] || !objectesDetectats[2]) ? 90 : -90; // preferencia esquerra
      rotate(avoidTurnDeg);
      moveForward();
      estat = APROPAMENT_AVOID_OBSTACLE;
      instructionSent = false;
    }
    break;

  case APROPAMENT_AVOID_OBSTACLE:
    bool sideClear = (avoidTurnDeg > 0) ? (objectesDetectats[2])
      : (objectesDetectats[0]);
    if (sideClear) {
      stopMotors();
      // Tornem a buscar la persona
      scanAngle = angleStartFromFOV();
      estat = APROPAMENT_SEARCH_PERSON;
    }
    else if (objectesDetectats[1]) {
      // Si hi ha obstacle frontal, intentem girar cap a l'altre costat
      stopMotors();
      avoidTurnDeg = (avoidTurnDeg > 0) ? -90 : 90;
      rotate(avoidTurnDeg);
      moveForward();
      estat = APROPAMENT_FORWARD_TO_OBSTACLE;
    }
    break;
  }
}

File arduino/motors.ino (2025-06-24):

void leftTick()
{
  leftEncoder.tick();
}

void rightTick()
{
  rightEncoder.tick();
}

void initMotors()
{
  delay(200);
  pinMode(LPWM1, OUTPUT);
  pinMode(LPWM2, OUTPUT);
  pinMode(RPWM1, OUTPUT);
  pinMode(RPWM2, OUTPUT);
  attachInterrupt(digitalPinToInterrupt(LEFT_CHA), leftTick, CHANGE);
  attachInterrupt(digitalPinToInterrupt(LEFT_CHB), leftTick, CHANGE);
  attachInterrupt(digitalPinToInterrupt(RIGHT_CHA), rightTick, CHANGE);
  attachInterrupt(digitalPinToInterrupt(RIGHT_CHB), rightTick, CHANGE);
  stopMotors();
}

void setLeft(bool dir, uint8_t PWM = rotatoryPWM)
{
  analogWrite(LPWM1, dir ? PWM : 0);
  analogWrite(LPWM2, dir ? 0 : PWM);
}

void setRight(bool dir, uint8_t PWM = rotatoryPWM)
{
  analogWrite(RPWM1, dir ? PWM : 0);
  analogWrite(RPWM2, dir ? 0 : PWM);
}

void moveForward()
{
  setLeft(true, linealPWM);
  setRight(true, linealPWM);
}

void stopMotors()
{
  analogWrite(LPWM1, 0);
  analogWrite(LPWM2, 0);
  analogWrite(RPWM1, 0);
  analogWrite(RPWM2, 0);
}

void resetEncoders()
{
  leftEncoder.setPosition(0);
  rightEncoder.setPosition(0);
}

long getLeftTicks()
{
  return abs(leftEncoder.getPosition());
}

long getRightTicks()
{
  return abs(rightEncoder.getPosition());
}

void rotate(float angleRad)
{
  resetEncoders();

  double arcLength = fabs(angleRad) * d * 2;
  double wheelCircumference = 2.0 * PI * r;
  double wheelRotations = arcLength / wheelCircumference;
  long targetTicks = (long)(wheelRotations * TICKS_PER_REV);

  bool rotateLeft = angleRad > 0;
  setLeft(rotateLeft);
  setRight(!rotateLeft);

  while (getLeftTicks() < targetTicks && getRightTicks() < targetTicks)
  {
    long left = getLeftTicks();
    long right = getRightTicks();
    // if(getButtons()==1) giraSeguent=ATURAT;
    // Serial.print("Target: ");
    // Serial.print(targetTicks);
    // Serial.print(" | L: ");
    // Serial.print(left);
    // Serial.print(" | R: ");
    // Serial.println(right);

    delay(50);
  }

  stopMotors();

  // Serial.print("Final L: ");
  // Serial.print(getLeftTicks());
  // Serial.print(" | Final R: ");
  // Serial.println(getRightTicks());
}

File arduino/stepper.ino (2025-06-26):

void initStepperCam() {
  pinMode(IN1, OUTPUT);
  pinMode(IN2, OUTPUT);
  pinMode(IN3, OUTPUT);
  pinMode(IN4, OUTPUT);
}

void moveSingleStep(int direction) {
  static int currentStep = 0;

  currentStep = (currentStep + direction + 8) % 8;

  digitalWrite(IN1, stepSequence[currentStep][0]);
  digitalWrite(IN2, stepSequence[currentStep][1]);
  digitalWrite(IN3, stepSequence[currentStep][2]);
  digitalWrite(IN4, stepSequence[currentStep][3]);

  delayMicroseconds(STEP_DELAY);
  absolutePosition += direction;
}

void rotateCamera(double targetAngle) {
  int targetSteps = round(targetAngle * STEPS_PER_REV / TWO_PI);

  int stepsToMove = targetSteps - absolutePosition;
  int direction = (stepsToMove > 0) ? 1 : -1;
  stepsToMove = abs(stepsToMove);

  for (int i = 0; i < stepsToMove; i++) {
    moveSingleStep(direction);
  }

  digitalWrite(IN1, LOW);
  digitalWrite(IN2, LOW);
  digitalWrite(IN3, LOW);
  digitalWrite(IN4, LOW);
}

void rotateCameraToCenter() {
  rotateCamera(0);
}

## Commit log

2025-05-03 Documentació + Connexió Arduino-Raspberry
2025-05-05 Commit de pipeline de YOLO. Falta acabar
2025-05-11 Commit de yolo con ejecución de modelObjectDetector
2025-05-11 Commit de arreglos
2025-05-11 Commit de reconeixer objectes 1
2025-05-13 Commit de pipeline de YOLO. con postprocesado
2025-05-15 Commit de Text-to-speech a revisar
2025-05-15 Commit funcional de reconeixer objectes
2025-05-19 Esquema elèctric afegit
    [esquema.fzz]
2025-05-23 Motors fet
2025-05-25 Estat PETICIÓ fet
2025-05-25 super commit de cloud run para modelos de YOLO
2025-05-26 IO Arduino Raspy canviat
2025-05-26 movimiento motor paso a paso
2025-05-27 cloud run con arreglos de despliegue
2025-05-29 Motors canviat pel nou chasis
2025-06-03 Avanç main Arduino
2025-06-04 Main Arduino -APROPAMENT
2025-06-04 copia de seguridad APIs
2025-06-05 main raspberry actualizado
2025-06-21 esquema actualitzat i imatge afegida
    [esquema.fzz]
2025-06-22 Canvi per millor cablejat
2025-06-24 Arreglats Motors + Distàncies + Botons
    [main.ino, motors.ino]
2025-06-25 flip image 180 degrees
    [pi_camera.py]
2025-06-25 Dissenys 3d afegits
    [Mango.stl, SoporteCamara.stl, SoporteMotorPasoAPaso.stl]
2025-06-25 stepper a main
2025-06-25 canvis en funcions camera
2025-06-25 Final Esquema Hardware
    [esquema.fzz]
2025-06-25 apropament arduino<-->raspi working
